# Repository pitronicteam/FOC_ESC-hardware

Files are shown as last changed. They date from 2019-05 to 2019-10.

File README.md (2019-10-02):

# FOC ESC HARDWARE
FOC(Field-Oriented Control) ESC is aimed at high-performance BLDC motor control.

The purpose of creating this repository is to share the hardware designs to:
1. Get feedback from the community and improve them;
2. Attract people that are interested in this and have the capability to join the software development.

## Advantages of FOC

- Independent, simple control of torque and flux
- Provide smooth torque over the entire speed range
- Provide rated torque near zero speed
- Speed up the dynamic process of acceleration and deceleration

- Reduce mechanical vibration caused by torque fluctuations
- Reduce noise
- Improve efficiency
- Improve speed accuracy and responsiveness

## Hardware Designs
Hardware designs delivered by the project are listed below. We use AD(Altium Designer) for design.

### Prototype PAC5523

Prototype PAC5523 is our first FOC ESC hardware design. More info [here](https://github.com/AirFleetTeam/FOC_ESC-hardware/blob/master/PAC5523/README.md).

### Prototype G431 4IN1

Prototype G431 4IN1 is a 30.5x30.5mm 4IN1 ESC which can be easily amounted on drones. This design uses STM32G431KBU6 QFN32 chips. Reference design from STM's B-G431B-ESC1. More info [here](https://github.com/AirFleetTeam/FOC_ESC-hardware/blob/master/STM32G431/README.md).

- 2 phase current
- High performance BEMF circuit
- Support up to 6s
- SPI communication
- 4 SK6812 RGB programmable LEDs

### Hall Sensor

For sensored FOC, we designed a hall sensor board.

## Commercial Use

This project is under GPLv3.0, all files are **FOR development ONLY**. For commercial use, please contact us.

## Getting Start

We are active in betaflight slack group, join us in #open_esc_firmware. 

Open the issues page and submit what you think to us.

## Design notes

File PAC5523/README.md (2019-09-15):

# Prototype PAC5523

CruxOne is our first FOC ESC hardware design. Originally from Active-semi PAC5523 EVK1 reference design.

[PAC5523](http://active-semi.com/products/intelligent-motor-control/pac5523) is a powerful MCU which intergrates build-in DCDC and MOSFET gate drivers.

- [I/O information](https://github.com/AirFleetTeam/FOC_ESC-hardware/blob/master/PAC5523/Pin_IO_assignments.md)
- [Schematic](https://github.com/AirFleetTeam/FOC_ESC-hardware/blob/master/PAC5523/CruxOne_v1.2_schematic.pdf)
- [PCB](https://github.com/AirFleetTeam/FOC_ESC-hardware/blob/master/PAC5523/CruxOne_v1.2.PcbDoc) 

## Detials

- 4 layers
- Supprot 2-6s input
- 3 phase current

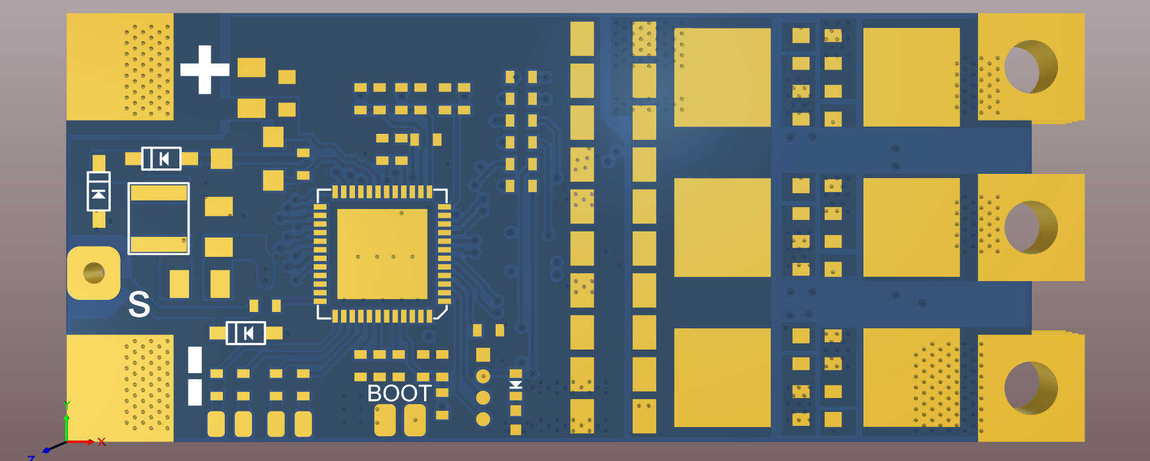
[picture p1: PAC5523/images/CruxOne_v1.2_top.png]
CruxOne_v1.2_top

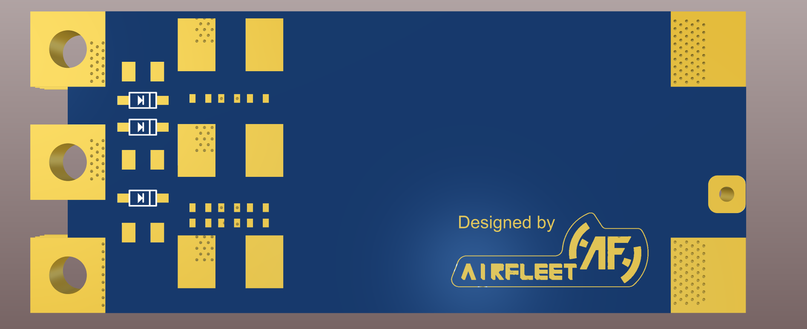
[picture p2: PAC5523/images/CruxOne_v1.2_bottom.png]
CruxOne_v1.2_bottom


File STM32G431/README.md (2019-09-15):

# Prototype G431 4IN1

Prototype G431 4IN1 is a 30.5x30.5mm 4IN1 ESC which can be easily amounted on drones. This design uses STM32G431KBU6 QFN32 chips. Reference design from STM's B-G431B-ESC1.

[STM32G431KUB6](https://www.st.com/content/st_com/en/products/microcontrollers-microprocessors/stm32-32-bit-arm-cortex-mcus/stm32-mainstream-mcus/stm32g4-series/stm32g4x1/stm32g431k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) is a chip based on M4 core. Due to the small number of pins on this chip, we cannot make it support CAN-FD on the basis of FOC pin map.

- [I/O information](https://github.com/AirFleetTeam/FOC_ESC-hardware/blob/master/STM32G431/Pin_IO_assignments.md)
- [Schematic](https://github.com/AirFleetTeam/FOC_ESC-hardware/blob/master/STM32G431/PROTOTYPE_G431_4IN1_v1.0.pdf)
- [PCB](https://github.com/AirFleetTeam/FOC_ESC-hardware/blob/master/STM32G431/PROTOTYPE_G431_4IN1_v1.0.PcbDoc)

## Details

- 8 layers (3oz| 3oz| 3oz| 3oz| 2oz| 2oz| 2oz| 2oz)
- 2 phase current
- High performance BEMF circuit
- Support up to 6s
- 4 SK6812 RGB programmable LEDs
- SPI communication

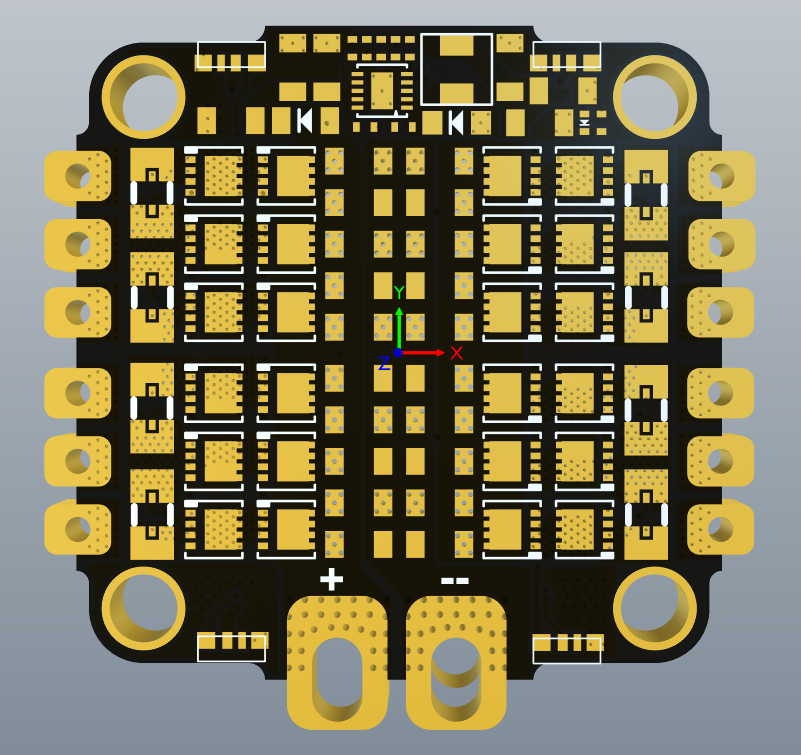
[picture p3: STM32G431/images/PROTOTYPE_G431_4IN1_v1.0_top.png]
CruxOne_v1.2_top

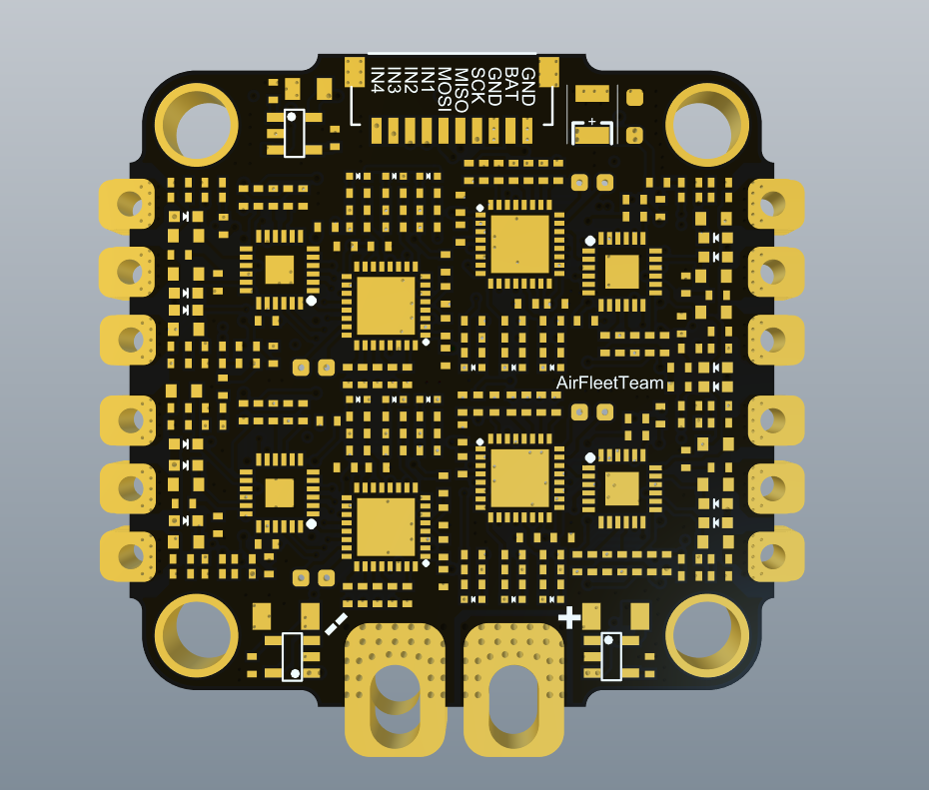
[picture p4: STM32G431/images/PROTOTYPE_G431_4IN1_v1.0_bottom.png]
CruxOne_v1.2_bottom


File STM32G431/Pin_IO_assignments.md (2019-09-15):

The following is the assignments of the pin：

PIN Number |PIN Name | Assignment |Note
:- |:- |:- |:-
1|VDD|+3V3
2|PF0-OSC_IN|TIM1_CH3N
3|PF1-OSC_OUT|BEMF3
4|PG10-NRST|NRST
5|PA0|V-BUS
6|PA1|OPAmp1+
7|PA2|NC
8|PA3|OPAmp1-
9|PA4|BEMF1
10|PA5|OPAmp2+
11|PA6|NC
12|PA7|OPAmp2-
13|PB0|BEMF2
14|VSSA|GND
15|VDDA|+3V3
16|VSS|GND
17|VDD|+3V3
18|PA8|TIM1_CH1
19|PA9|TIM1_CH2
20|PA10|TIM1_CH3
21|PA11|TIM1_CH1N
22|PA12|TIM1_CH2N
23|PA13|SWDIO
24|PA14|SWCLK
25|PA15|SPI1_NSS|Chip select
26|PB3|SPI1_SCK
27|PB4|SPI1_MISO
28|PB5|SPI1_MOSI
29|PB6|LED
30|PB7|GPIO_BEMF
31|PB8-BOOT0|BOOT
32|VSS|GND

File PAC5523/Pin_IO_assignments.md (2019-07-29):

The following is the assignments of the pin：

PIN Number |PIN Name | Assignment |Note
:- |:- |:- |:-
0|EP(VSS)|GND|Bottom pad
1 | PF1 | NC |
2|PF1|SWDIO|
3|PF0|SWCLK|
4|VCC33||3V3
5|AIO0|IA_B|
6|AIO1|IA_A|
7|AIO2|IB_B|
8|AIO3|IB_A|
9|AIO4|IC_B|
10|AIO5|IC_A|
11|AIO6|BOOT|Push button input
12|AIO7|OUTA|
13|AIO8|OUTB|
14|AIO9|OUTC|
15|VSYS|5V|5V System power supply
16|REG0||System regulator output
17|CSM||Switching supply current sense input
18|VP||Main power supply
19|VHM|VCC_IN|Same as BAT_IN
20|DRM||Switching supply driver output
21|DRL0|A_DRV_LO|
22|DRL1|B_DRV_LO|
23|DRL2|C_DRV_LO|
24|DRS3|OUTA|
25|DRH3|A_DRV_HI|
26|DRB3|VP|
27|DRS4|OUTB|
28|DRH4|B_DRV_HI|
29|DRB4|VP|
30|DRS5|OUTC|
31|DRH5|C_DRV_HI|
32|DRB5|VP|
33|PC7|NC|
34|PC4|NC|
35|PC5|NC|
36|PC6|RC_IN|
37|PE0|PE0|
38|PE1|PE1|
39|PE2|PE2|
40|PE3|PE3|
41|VCC18||Internally generated 1V8 power supply
42|VCORE||Internally generated 1V2 core power supply
43|VSS|GND|
44|VCCIO||Internally generated digital I/O 3V3 power supply
45|PF6/AD6|BAT_IN|Same as VCC_IN
46|PF5/AD5|NC|
47|PF4/AD4|NC|
48|PF3|NC|

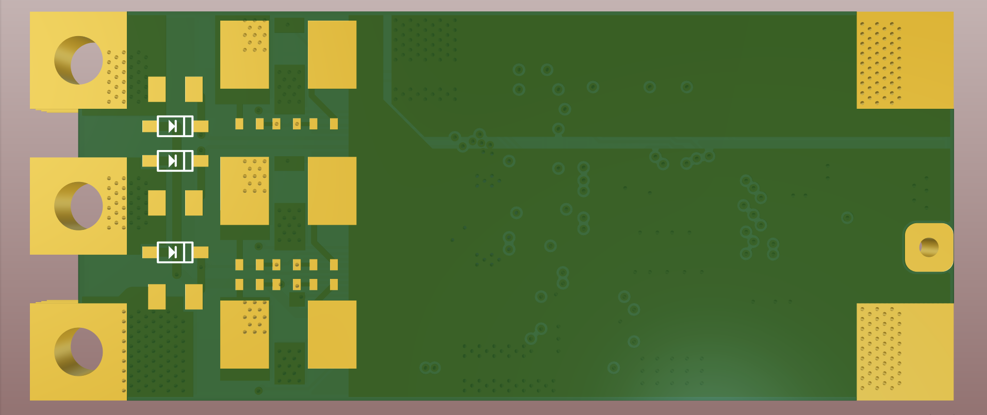
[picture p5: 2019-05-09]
PAC5523/images/FOC_ESC_v1.1_bottom.png

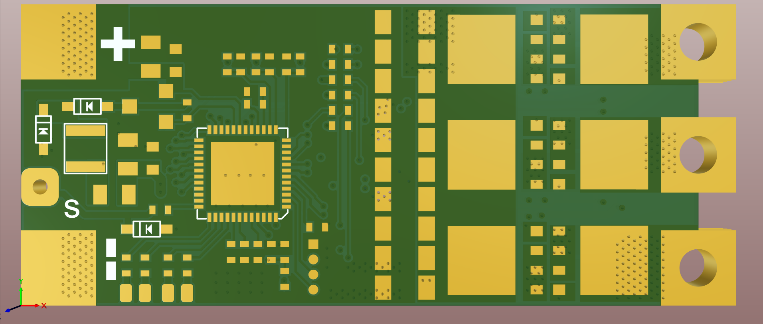
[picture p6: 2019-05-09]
PAC5523/images/FOC_ESC_v1.1_top.png

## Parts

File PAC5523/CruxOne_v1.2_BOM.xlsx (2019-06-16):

Comment | Description | Designator | Footprint | LibRef | Quantity
 |  | A1, A2, A3 | PAD-1 4*3 | PAD | 3
0.1uF/25V |  | C1 | 0603-RES | Cap | 1
2.2uF/50V |  | C2 | 0805-RES | Cap | 1
22uF/35V |  | C3, C4, C5, C6, C7, C8, C9, C10, C25, C26 | 1206-RES | C | 10
332 |  | C11, C23, C24 | 0402-RES | Cap | 3
10uF/25V |  | C12 | 0805-RES | Cap | 1
0.1uF/16V |  | C13 | 0402-RES | Cap | 1
1uF/25V |  | C14, C19, C22 | 0805-RES | Cap | 3
4.7uF/6.3V |  | C15, C20 | 0402-RES | Cap | 2
2.2uF/6.3V |  | C16, C17, C18 | 0402-RES | Cap | 3
0.1uF/25V |  | C21 | 0402-RES | Cap | 1
T4 |  | D1, D2, D3, D4, D5 | SOD323 | Diode | 5
3V3 TVS |  | D6 | SOD323 | Diode | 1
BAT |  | J1 | PAD-1 4*3 | PAD | 1
GND |  | J2 | PAD-1 4*3 | PAD | 1
RC_IN |  | J3 | PAD-1 2*1.5 | PAD | 1
SWD |  | J4 | 1.0-4p | J_4P | 1
PAD |  | J5, J6, J7, J8 | PAD-1 0.8*1.2 | PAD | 4
BOOT |  | J9 | PAD-1 1*1.5 | PAD | 1
GND |  | J10 | PAD-1 1*1.5 | PAD | 1
LCF1008-150K-T |  | L1 | LCF1008-RES | R | 1
RED |  | LED1 | 0402-LED | LED1 | 1
SI2308 |  | Q1 | SOT-23 | P-MOS | 1
NTMFS5C430NL |  | Q2, Q3, Q4, Q5, Q6, Q8 | DFN5*6 | AON7418 | 6
10R |  | R1, R4, R10, R16, R22, R29 | 0402-RES | R | 6
100R |  | R2, R5, R8, R13 | 0402-RES | R | 4
1K |  | R3, R26 | 0402-RES | R | 2
0.33R |  | R6 | 0805-RES | R | 1
100R 1% |  | R7, R12, R23, R27, R32, R36 | 0402-RES | R | 6
0.001R |  | R9, R25, R34 | 2512-RES | R | 3
51R |  | R11 | 0402-RES | R | 1
47K |  | R15, R31, R33, R35 | 0402-RES | R | 4
2K |  | R18, R37, R38, R39 | 0402-RES | R | 4
330R |  | R? | 0402-CAP | R | 1
PCA5523 |  | U1 | QFN48 | PCA5523 | 1

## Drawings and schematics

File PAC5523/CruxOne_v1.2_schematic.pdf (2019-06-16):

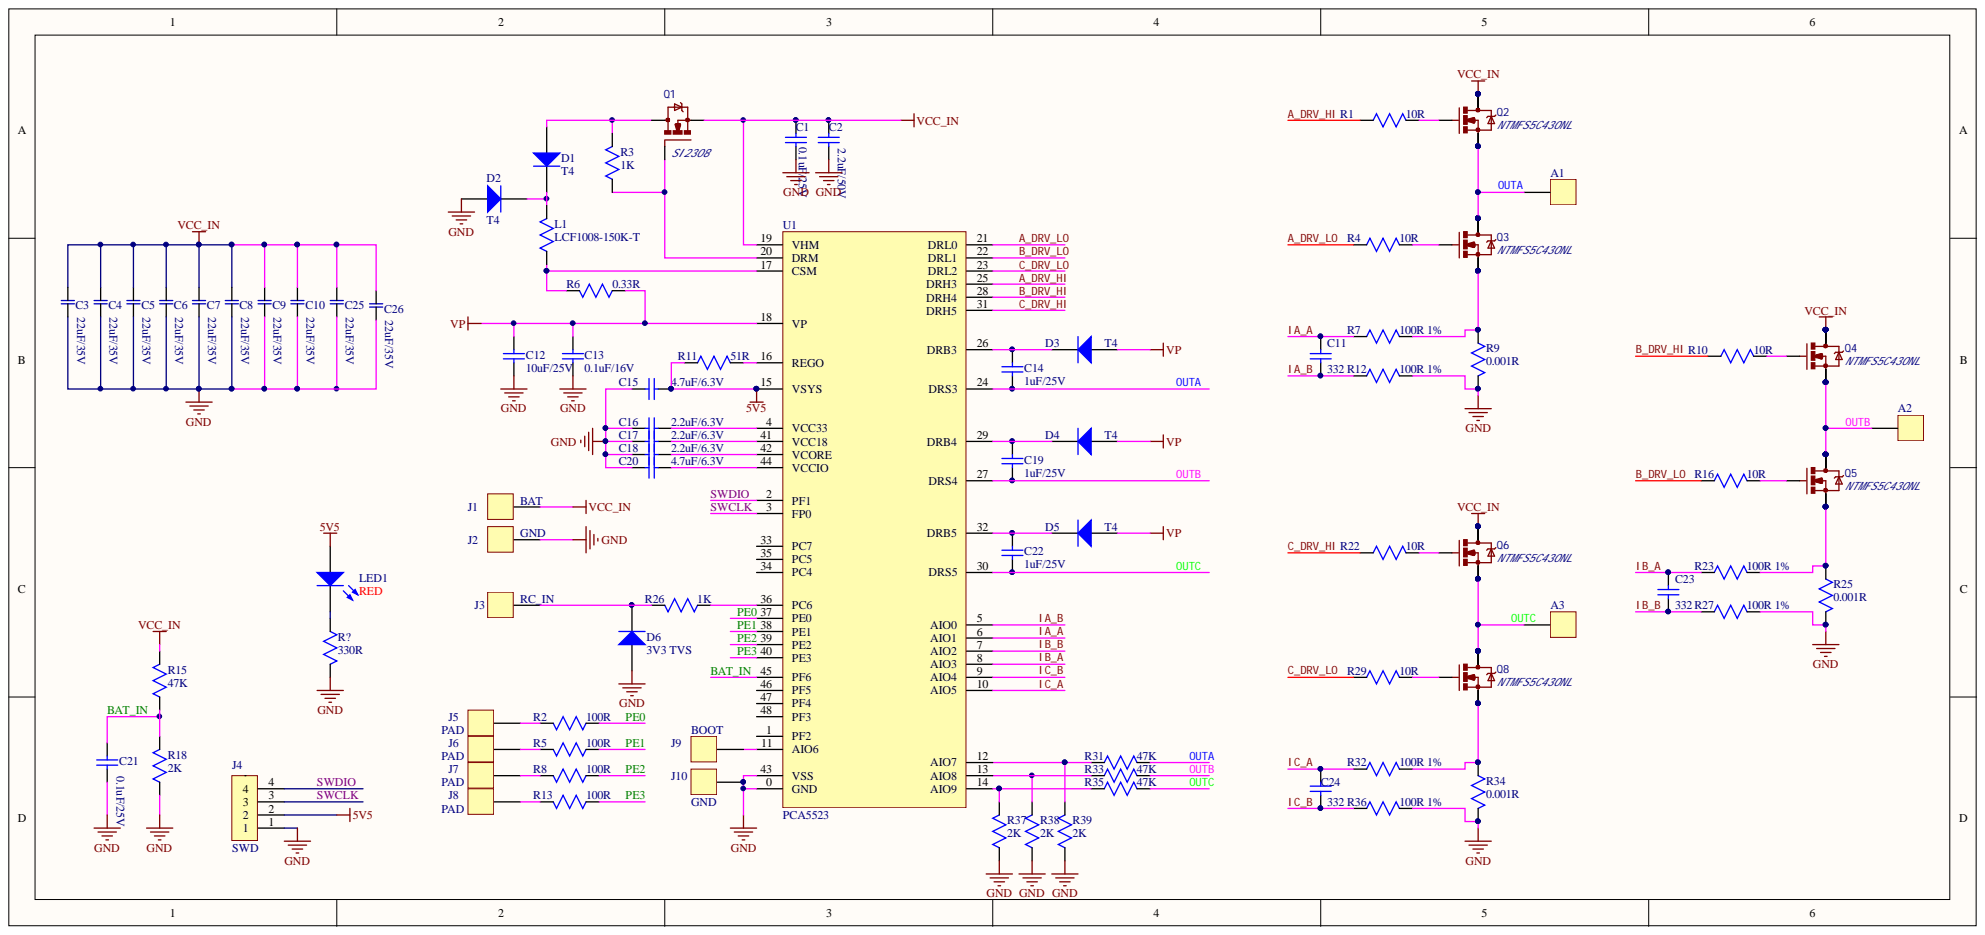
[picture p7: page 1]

C1 | 8 | V GND 2 . 2 u F/6 . 3 4 2

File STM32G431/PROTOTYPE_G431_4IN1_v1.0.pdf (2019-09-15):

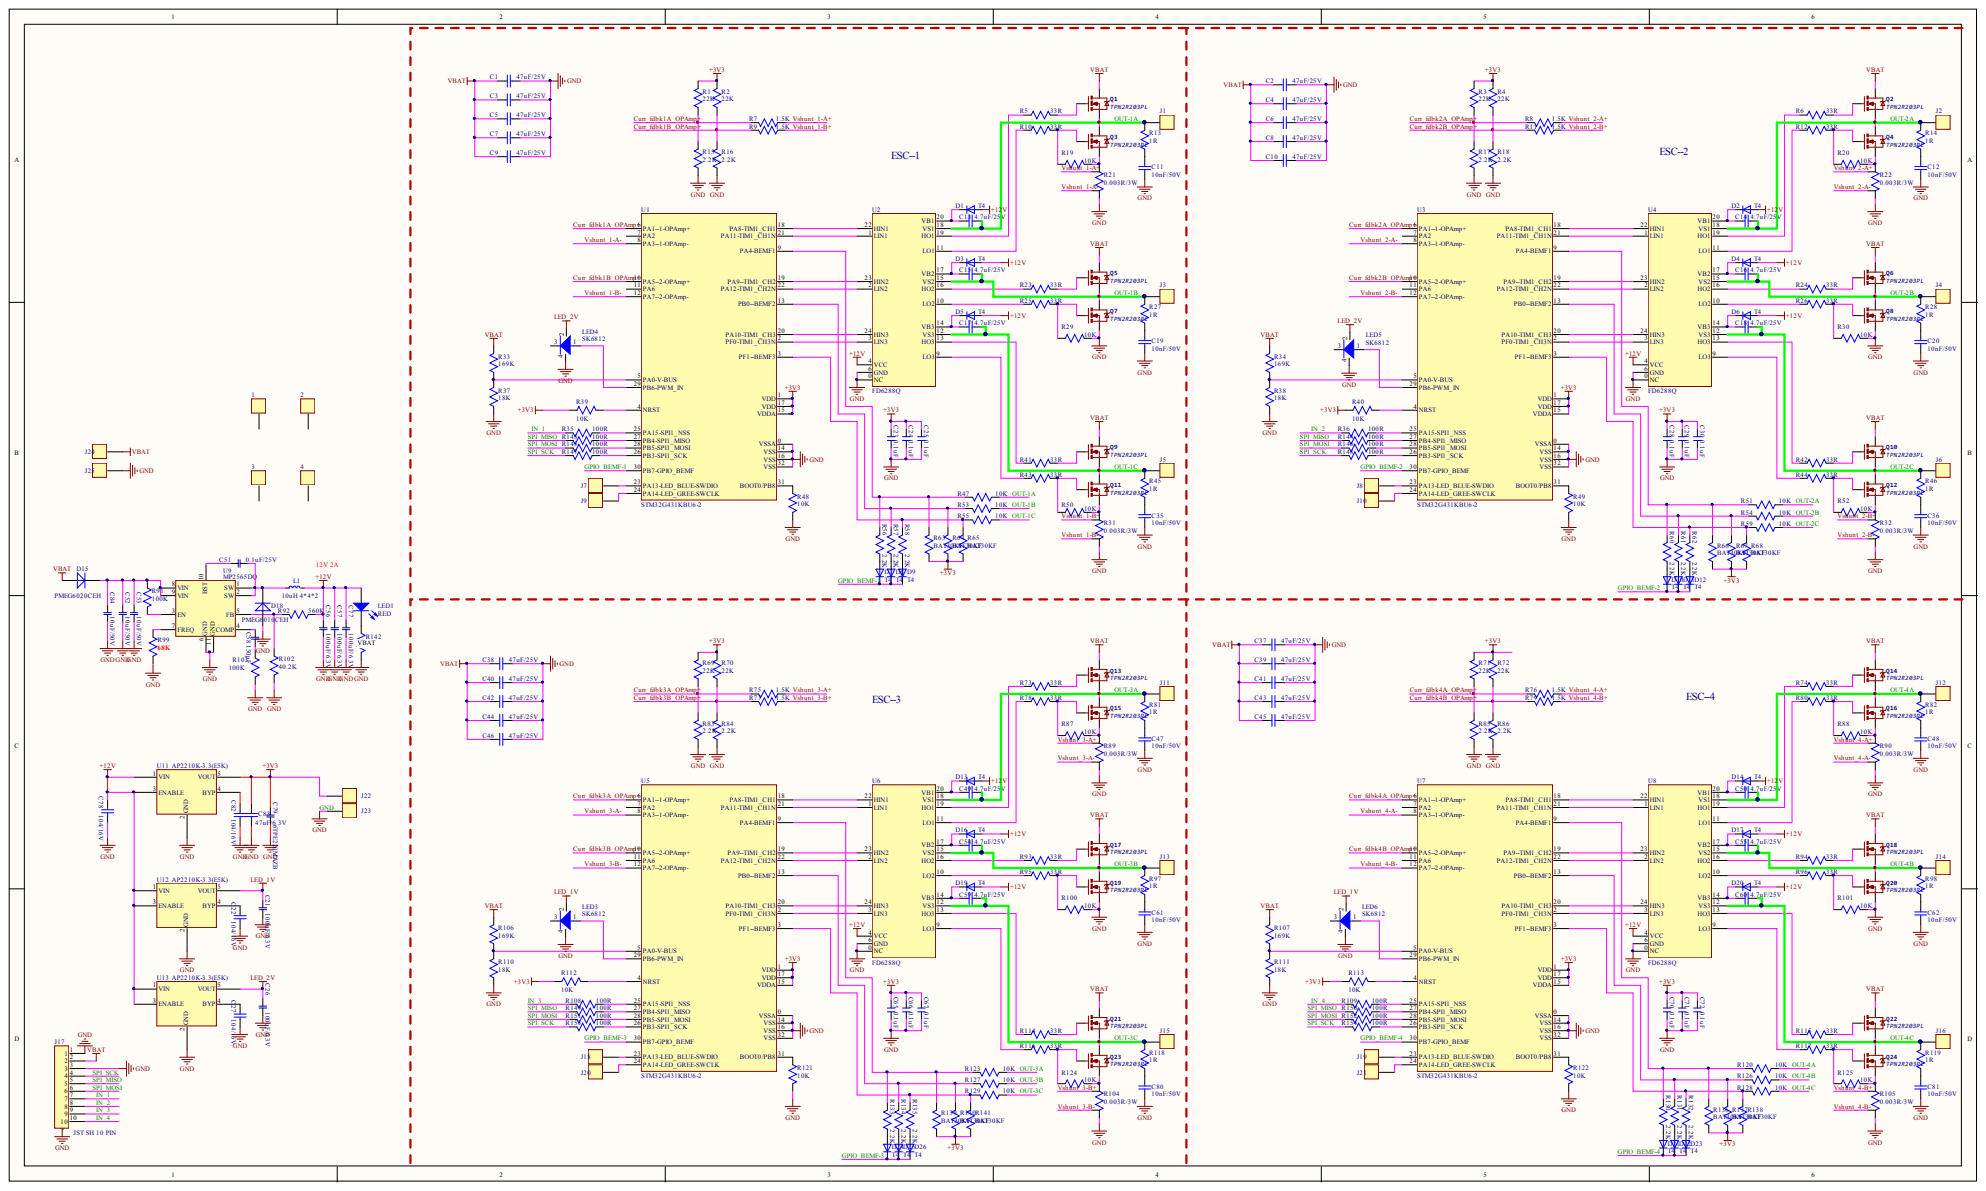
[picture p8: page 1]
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

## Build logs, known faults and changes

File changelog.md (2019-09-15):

# Change LOG

## 09/15/2019-File structure clean up

+ Add a new hardware design based on STM32G431.
+ Clean up the old file structure.

## 06/16/2019-v1.2 Changes from v1.1.x
+ Named the board as CruxOne
+ Fixed some bugs to avoid incorrect processing when producing PCBs.
+ Added a boot pad broke from AIO6 (hold 8s to reset) .
+ Added an LED to indicate the working status of VSYS.
+ Added a logo.
+ Removed NC 3V3 from SWD connector, replace it with 5V (according to the datasheet, 3v3 can't initialize the microcontroller but 5V can) .

And as always, screenshots of PCB with silksreen shown as below:

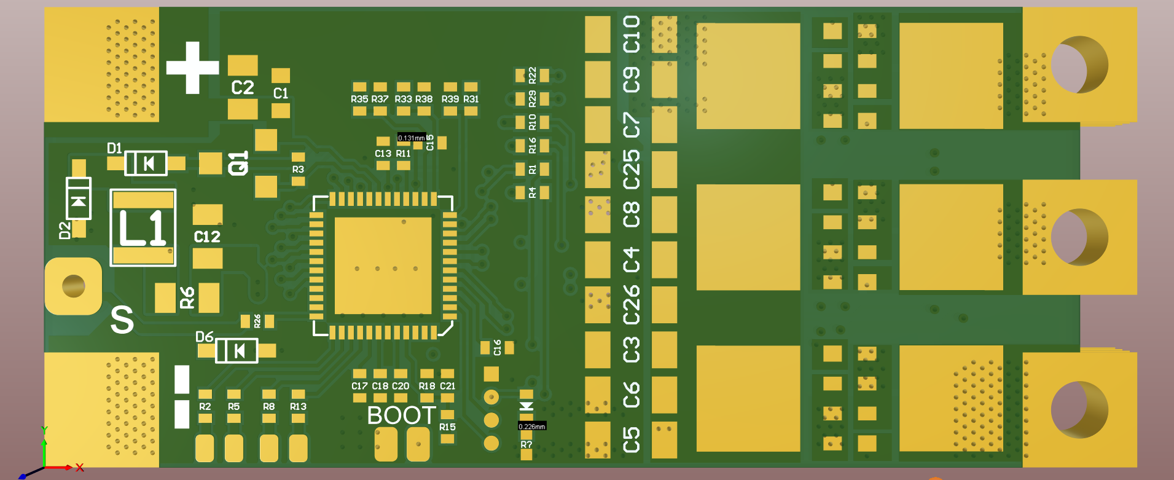
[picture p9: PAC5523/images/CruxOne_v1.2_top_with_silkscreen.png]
CruxOne_v1.2_top_with_silkscreen

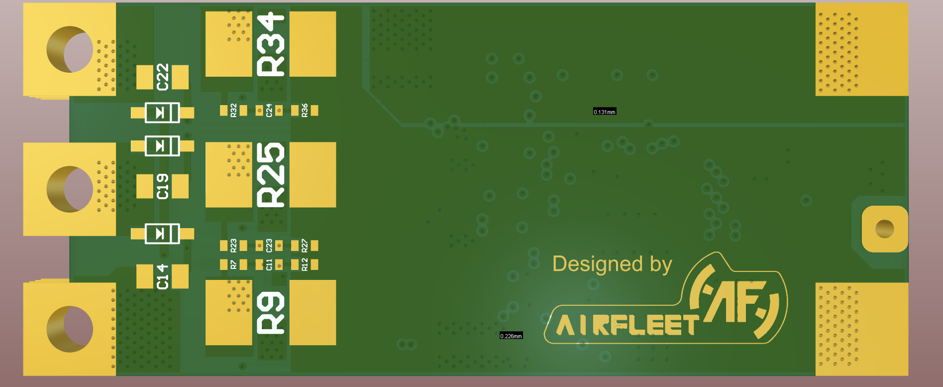
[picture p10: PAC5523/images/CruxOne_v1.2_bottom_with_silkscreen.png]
CruxOne_v1.2_bottom_with_silkscreen


## 05/26/2019-v1.1.1 Changes from v1.1
+ Added silkscreens for almost all components
+ Added two screenshots for quick review

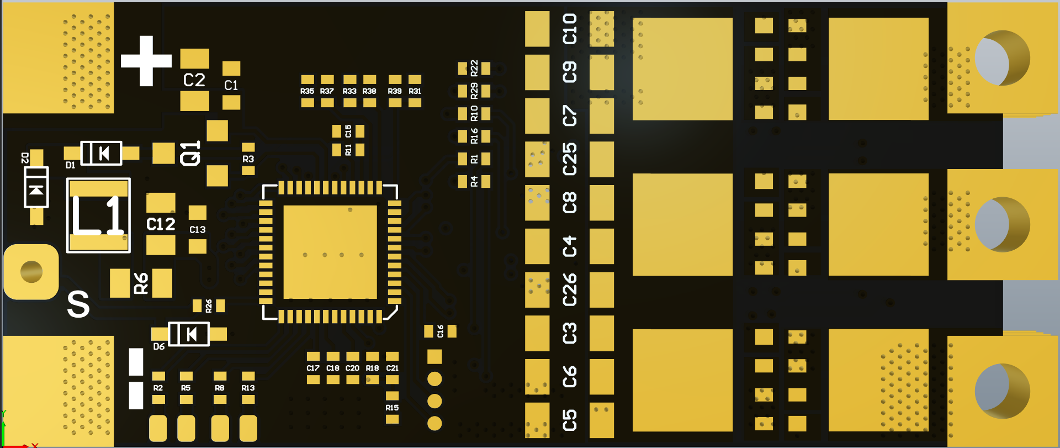
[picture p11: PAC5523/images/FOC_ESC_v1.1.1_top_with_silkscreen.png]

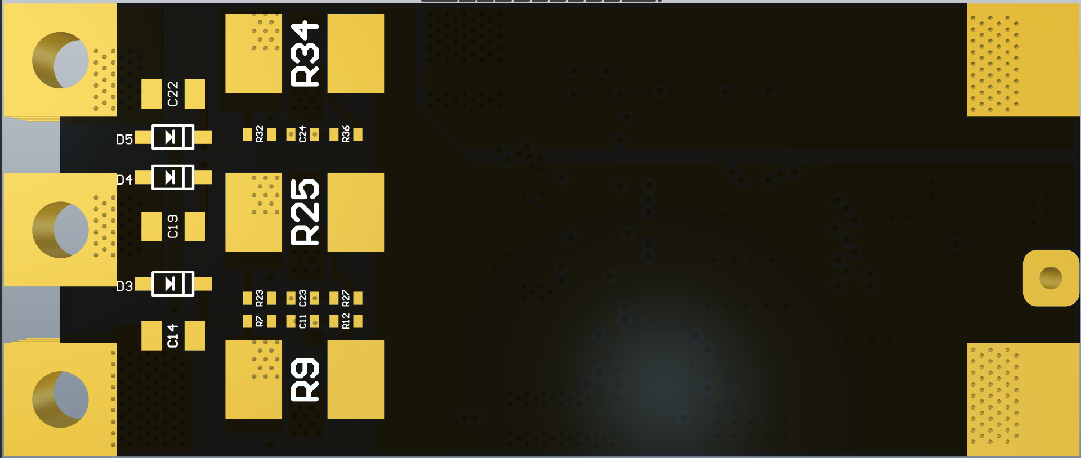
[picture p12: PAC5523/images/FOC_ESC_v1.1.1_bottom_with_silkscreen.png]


## 05/09/2019-v1.1 Changes from v1.0
+ Added a TVS diode across input
+ Removed MOSFETs' pulldown resistors
+ Added some test points
+ Broke out serial interface
+ Redesigned the layout of electronic components
+ Reduced the number of layers to 4

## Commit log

2019-04-27 upload files via github desktop
    [FOC_ESC V1.0.PcbDoc, FOC_ESC V1.0.SchDoc]
2019-05-08 Update schematic to v1.1
    According to issues#2,#3,#4,#5,#6. And add a BOM.
2019-05-09 Update v1.1 pcb files
    Some circuits were changed according to the schematic v1.1.
    Change the MCU and MOS to the same side, and reduce the number of layers to 4 layers.
    [FOC_ESC V1.0.PcbDoc, FOC_ESC V1.0.SchDoc, FOC_ESC V1.1.PcbDoc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]
2019-05-17 Upload hall sensor
    Designed by PDW
    [MA700 24mm.drl, MA700 24mm_copper_bottom.gbr, MA700 24mm_copper_top.gbr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]
2019-05-26 Upload a duplication
    This duplication shows all silkscreen of the components, which is convenient for hand soldering.
    [FOC_ESC V1.1.1_with_component_silkscreen.PcbDoc, FOC_ESC V1.1.PcbDoc]
2019-05-26 Upload two images
    Which is for hand soldering use
2019-05-26 Update FOC_ESC V1.1.1_with_component_silkscreen.PcbDoc
    [FOC_ESC V1.1.1_with_component_silkscreen.PcbDoc]
2019-06-16 Update version to 1.2
    For more information, check changelog.md.
    [CruxOne_v1.2.PcbDoc, CruxOne_v1.2.PrjPCB, CruxOne_v1.2.SchDoc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]
2019-09-15 File structure clean up
    [CruxOne_v1.2.PcbDoc, CruxOne_v1.2.PrjPCB, CruxOne_v1.2.SchDoc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]
2019-09-15 Update README for PAC5523 board
2019-09-15 Update README for G431 board
